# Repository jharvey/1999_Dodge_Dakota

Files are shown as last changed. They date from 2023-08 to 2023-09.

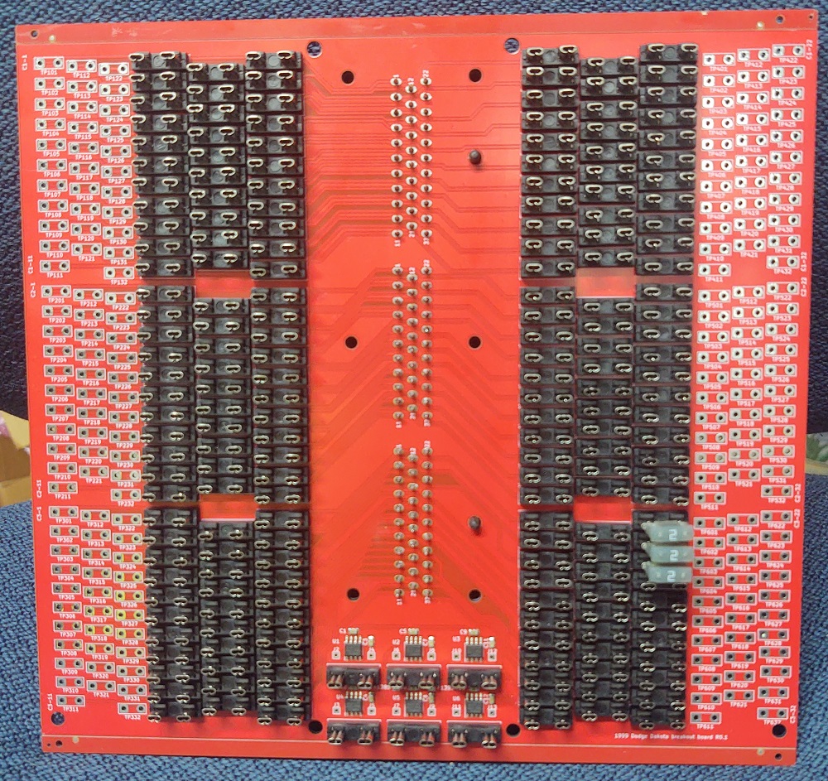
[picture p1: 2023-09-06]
export/Breakout/V0.1/Pictures/Fuse_Side_1000wide.jpg

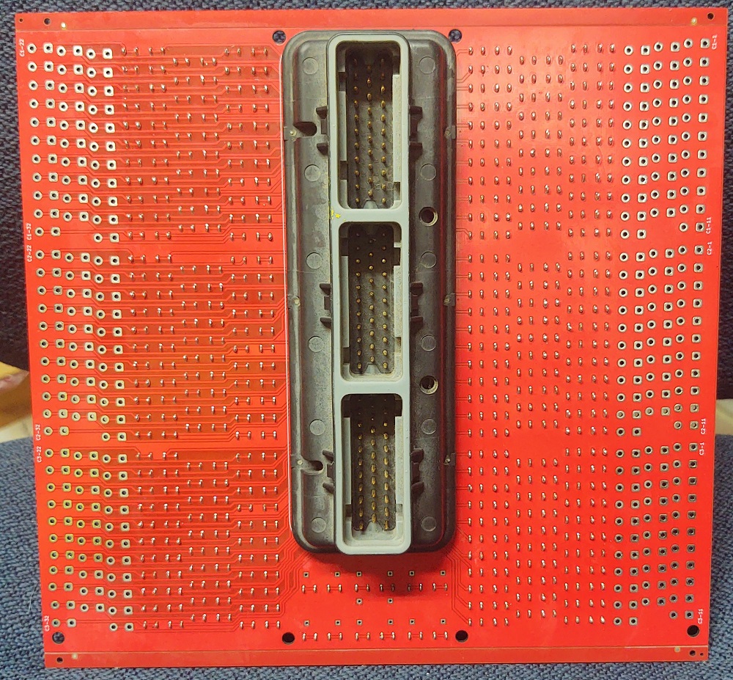
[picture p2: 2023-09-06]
export/Breakout/V0.1/Pictures/Connector_Side_1000wide.jpg

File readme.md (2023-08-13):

#  1999 Dodge Dakota, based on rusEFI PROTEUS

A high-featured board compatible with [rusEFI](https://github.com/rusefi/rusefi) firmware.

# Goals 

- Run my 1999 Dodge Dakota with factory harness and equipment
- Run a sequential ignition, quad-VVT v12 engine (eight injectors, eight ignition, five hall sensors, four VVT actuators, single throttles)
- Easily manufactured sealed enclosure (all connectors mount in-plane)
- Extensible for knock sensing

# Hardware Features

## Microcontroller

- STM32F429ZG
    - 180 MHz ARM Cortex-M7
    - 1MB flash
    - 256 KB SRAM
    - LQFP144 package

- Also fully compatible with several STM32F7 parts, including the STM32F767ZI, used on v0.1 and v0.2, as well as STM32F429ZIT6.

## Connectors
Factory connector for most wiring with TE Connectivity AMPSEAL connector(s) for upgrades:

- 2x 35 pin connectors
    - Board: TE 776231-1 (black, right) and 776231-2 (white, left)
    - Plug: TE 776164-1 (black, right) and 776164-2 (white, left)
- 1x 23 pin connector
    - Board: TE 776228-1
    - Plug: TE 770680-1
- 770854-1 terminals    

## Connectivity

- 1 mbit/s CAN bus
- USB 2.0 full speed (12 mbit/s), on-board or wired to connector for sealed applications
- [10-pin, 1.27mm Cortex debug header](http://infocenter.arm.com/help/topic/com.arm.doc.faqs/attached/13634/cortex_debug_connectors.pdf)

## Outputs
TBD
- 16x 4A low-side drivers
- 12x 5v ignition (or general purpose) outputs
- Dual H-bridges for electronic throttle (also supports stepper idle valve!)
- 4x 12v 3A high-side outputs

## Inputs
TBD
- 11x Analog voltage inputs
- 4x Analog temperature (5v pullup) inputs
- 2x VR crank/cam/vehicle speed inputs
- 6x hall cam/crank or digital input

## Power Supply

- Full operation from 6-24v supply
- Limited operation from 4-6v
- Dual 5v sensor supplies, 150mA each, fully protected
- Dual protected 12v external sensor supply

## Extensibility

- 10-pin internal header for knock expansion board.  We aren't confident in any one knock sensing design yet, so it's most useful to be able to swap it out without replacing the whole ECU.

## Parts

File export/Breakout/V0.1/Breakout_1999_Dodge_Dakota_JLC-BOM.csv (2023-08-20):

Comment | Designator | Footprint | LCSC
100nf | C1,C2,C5,C6,C9,C10 | Capacitor_SMD:C_0805_2012Metric | C49678
1nf | C3,C4,C7,C8,C11,C12 | Capacitor_SMD:C_0805_2012Metric | C46653
Fuse | F1001,F1002,F1003,F1004,F1005,F1006,F1007,F1008,F1009,F1010,F1011,F1012,F1013,F1014,F1015,F1016,F1017,F1018,F1019,F1020,F1021,F1022,F1023,F1024,F1025,F1026,F1027,F1028,F1029,F1030,F1031,F1032,F1033,F1034,F1035,F1036,F1037,F1038,F1039,F1040,F1041,F1042,F1043,F1044,F1045,F1046,F1047,F1048,F1049,F1050,F1051,F1052,F1053,F1054,F1055,F1056,F1057,F1058,F1059,F1060,F1061,F1062,F1063,F1064,F1065,F1066,F1067,F1068,F1069,F1070,F1071,F1072,F1073,F1074,F1075,F1076,F1077,F1078,F1079,F1080,F1081,F1082,F1083,F1084,F1085,F1086,F1087,F1088,F1089,F1090,F1091,F1092,F1093,F1094,F1095,F1096,F1097,F1098,F1099,F1100,F1101,F1102,F1103,F1104,F1105,F1106,F1107,F1108,F1109,F1110,F1111,F1112,F1113,F1114,F1115,F1116,F1117,F1118,F1119,F1120,F1121,F1122,F1123,F1124,F1125,F1126,F1127,F1128,F1129,F1130,F1131,F1132,F1133,F1134,F1135,F1136,F1137,F1138,F1139,F1140,F1141,F1142,F1143,F1144,F1145,F1146,F1147,F1148,F1149,F1150,F1151,F1152,F1153,F1154,F1155,F1156,F1157,F1158,F1159,F1160,F1161,F1162,F1163,F1164,F1165,F1166,F1167,F1168,F1169,F1170,F1171,F1172,F1173,F1174,F1175,F1176,F1177,F1178,F1179,F1180,F1181,F1182,F1183,F1184,F1185,F1186,F1187,F1188,F1189,F1190,F1191,F1192 |  | C151093
Fuse_Holder | F101,F102,F103,F104,F105,F106,F107,F108,F109,F110,F111,F112,F113,F114,F115,F116,F117,F118,F119,F120,F121,F122,F123,F124,F125,F126,F127,F128,F129,F130,F131,F132,F201,F202,F203,F204,F205,F206,F207,F208,F209,F210,F211,F212,F213,F214,F215,F216,F217,F218,F219,F220,F221,F222,F223,F224,F225,F226,F227,F228,F229,F230,F231,F232,F301,F302,F303,F304,F305,F306,F307,F308,F309,F310,F311,F312,F313,F314,F315,F316,F317,F318,F319,F320,F321,F322,F323,F324,F325,F326,F327,F328,F329,F330,F331,F332,F401,F402,F403,F404,F405,F406,F407,F408,F409,F410,F411,F412,F413,F414,F415,F416,F417,F418,F419,F420,F421,F422,F423,F424,F425,F426,F427,F428,F429,F430,F431,F432,F501,F502,F503,F504,F505,F506,F507,F508,F509,F510,F511,F512,F513,F514,F515,F516,F517,F518,F519,F520,F521,F522,F523,F524,F525,F526,F527,F528,F529,F530,F531,F532,F601,F602,F603,F604,F605,F606,F607,F608,F609,F610,F611,F612,F613,F614,F615,F616,F617,F618,F619,F620,F621,F622,F623,F624,F625,F626,F627,F628,F629,F630,F631,F632,F1193,F1194,F1195,F1196,F1197,F1198 | LCSC_parts:LCSC_C2935870_Fuse_holder | C2935870
Pig_Con | J2,J3,J4,J5,J6,J7,J8,J9,J10,J11,J12,J13,F1385,F1393 | TestPoint:TestPoint_THTPad_1.5x1.5mm_Drill0.7mm | NA
Dodge_Con | J1 | Dodge_Cons:1999_Dodge_Connector_32x3cons | NA
TestPoint_2Pole | TP101,TP102,TP103,TP104,TP105,TP106,TP107,TP108,TP109,TP110,TP111,TP112,TP113,TP114,TP115,TP116,TP117,TP118,TP119,TP120,TP121,TP122,TP123,TP124,TP125,TP126,TP127,TP128,TP129,TP130,TP131,TP132,TP201,TP202,TP203,TP204,TP205,TP206,TP207,TP208,TP209,TP210,TP211,TP212,TP213,TP214,TP215,TP216,TP217,TP218,TP219,TP220,TP221,TP222,TP223,TP224,TP225,TP226,TP227,TP228,TP229,TP230,TP231,TP232,TP301,TP302,TP303,TP304,TP305,TP306,TP307,TP308,TP309,TP310,TP311,TP312,TP313,TP314,TP315,TP316,TP317,TP318,TP319,TP320,TP321,TP322,TP323,TP324,TP325,TP326,TP327,TP328,TP329,TP330,TP331,TP332,TP401,TP402,TP403,TP404,TP405,TP406,TP407,TP408,TP409,TP410,TP411,TP412,TP413,TP414,TP415,TP416,TP417,TP418,TP419,TP420,TP421,TP422,TP423,TP424,TP425,TP426,TP427,TP428,TP429,TP430,TP431,TP432,TP501,TP502,TP503,TP504,TP505,TP506,TP507,TP508,TP509,TP510,TP511,TP512,TP513,TP514,TP515,TP516,TP517,TP518,TP519,TP520,TP521,TP522,TP523,TP524,TP525,TP526,TP527,TP528,TP529,TP530,TP531,TP532,TP601,TP602,TP603,TP604,TP605,TP606,TP607,TP608,TP609,TP610,TP611,TP612,TP613,TP614,TP615,TP616,TP617,TP618,TP619,TP620,TP621,TP622,TP623,TP624,TP625,TP626,TP627,TP628,TP629,TP630,TP631,TP632 | TestPoint:TestPoint_2Pads_Pitch5.08mm_Drill1.3mm | NA
ACS712xLCTR-20A | U1,U2,U3,U4,U5,U6 | Package_SO:SOIC-8_3.9x4.9mm_P1.27mm | C10681

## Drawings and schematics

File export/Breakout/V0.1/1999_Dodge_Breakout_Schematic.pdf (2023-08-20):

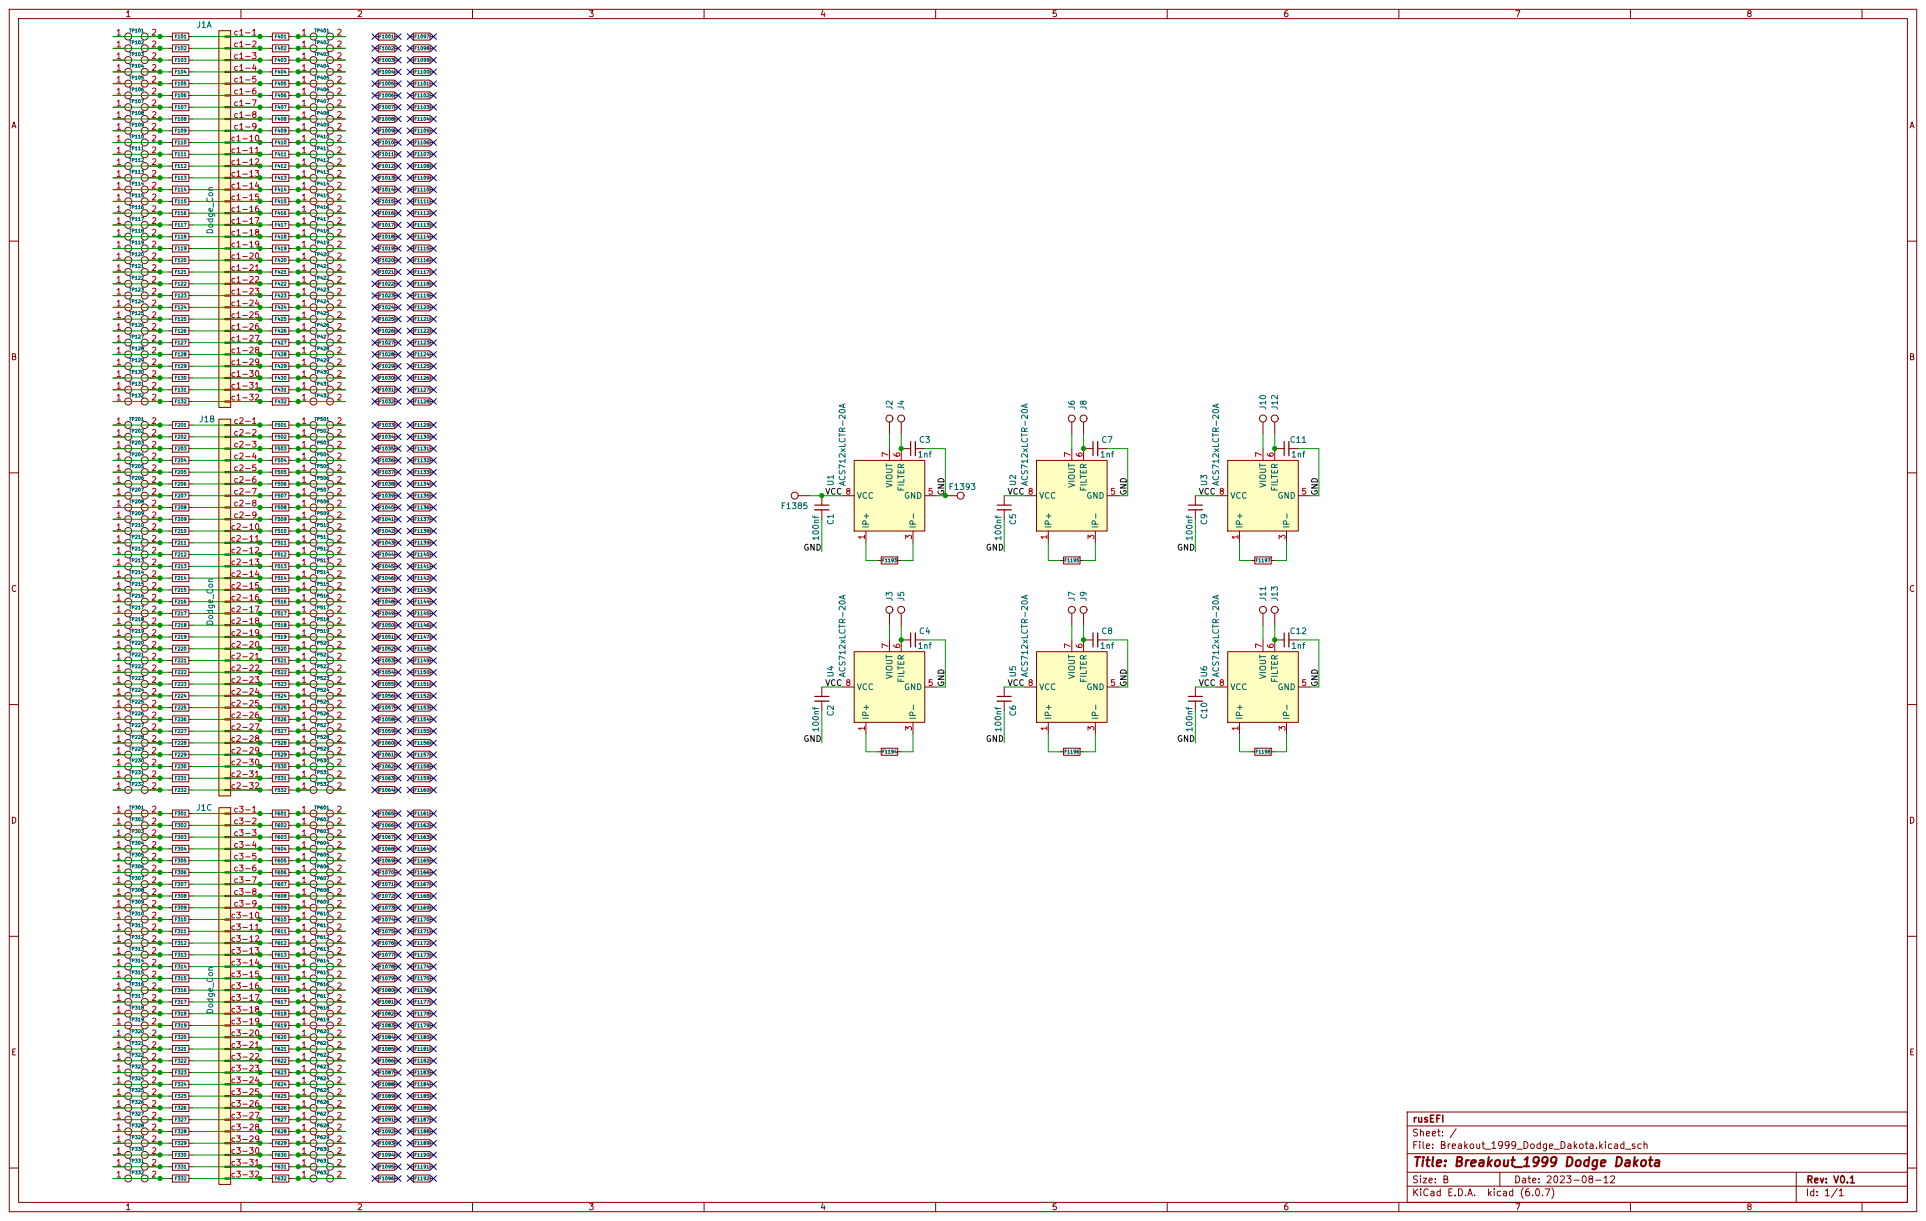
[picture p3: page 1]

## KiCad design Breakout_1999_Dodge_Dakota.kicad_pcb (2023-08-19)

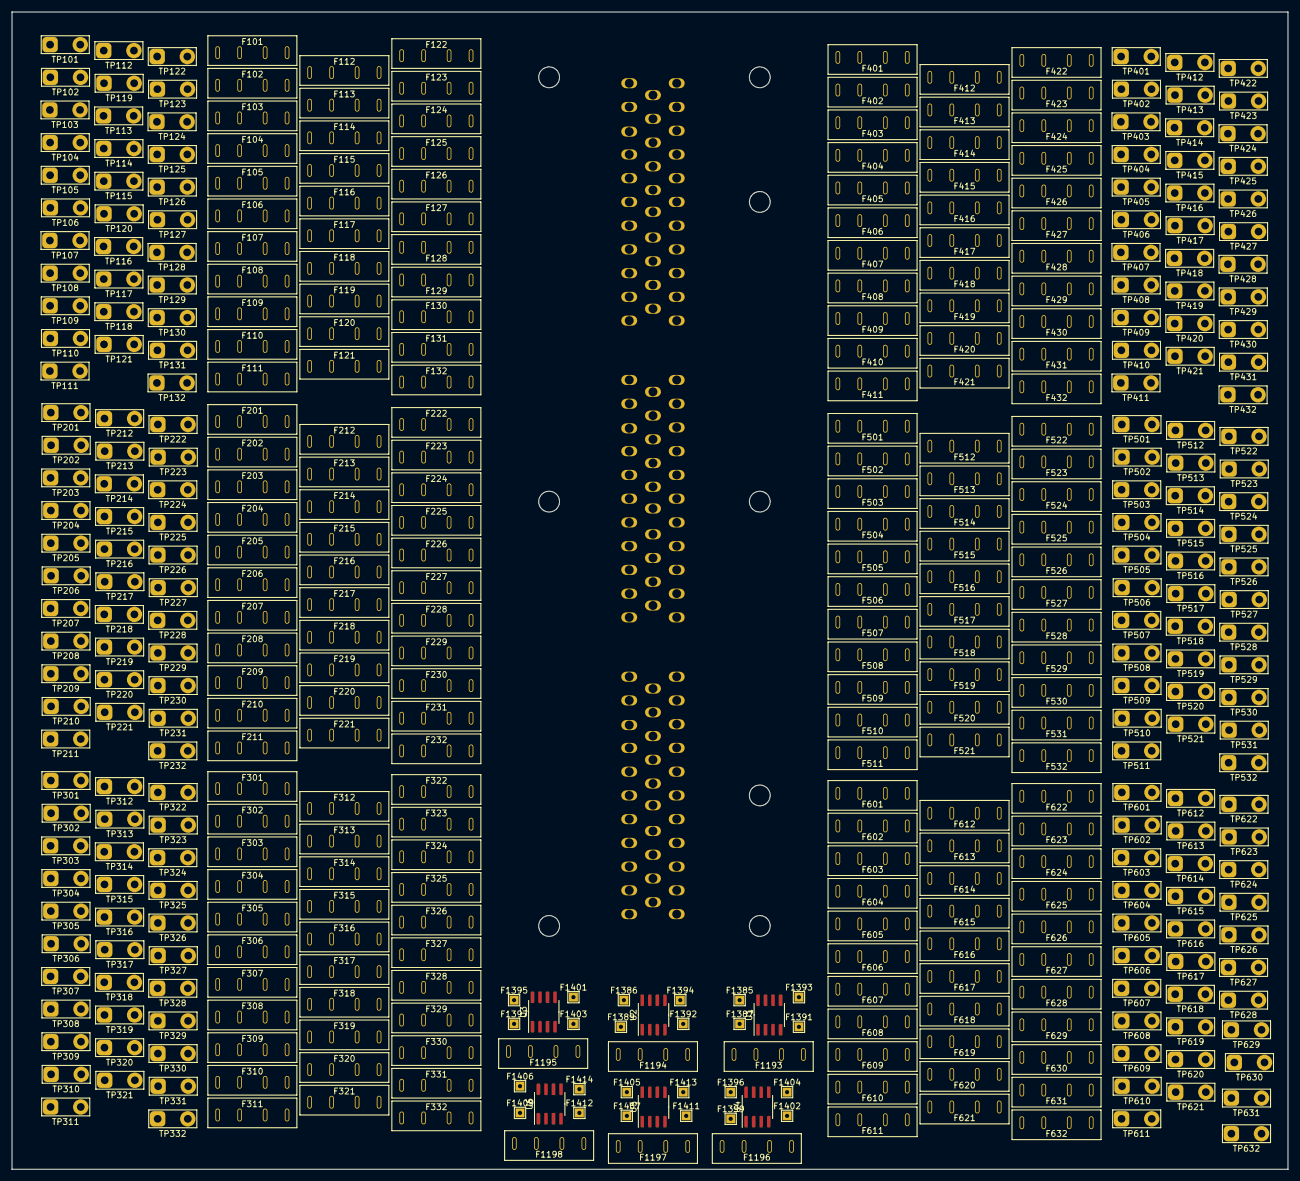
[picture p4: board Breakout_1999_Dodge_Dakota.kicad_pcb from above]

Board: 4 copper layers, 215.0 x 195.0 mm, 421 parts (1 on the bottom side), 324 nets, no tracks yet.

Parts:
F101, F102, F103, F104, F105, F106, F107, F108, F109, F110, F111, F112, F113, F114, F115, F116, F117, F118, F119, F120, F121, F122, F123, F124, F125, F126, F127, F128, F129, F130, F131, F132, F201, F202, F203, F204, F205, F206, F207, F208, F209, F210, F211, F212, F213, F214, F215, F216, F217, F218, F219, F220, F221, F222, F223, F224, F225, F226, F227, F228, F229, F230, F231, F232, F301, F302, F303, F304, F305, F306, F307, F308, F309, F310, F311, F312, F313, F314, F315, F316, F317, F318, F319, F320, F321, F322, F323, F324, F325, F326, F327, F328, F329, F330, F331, F332, F401, F402, F403, F404, F405, F406, F407, F408, F409, F410, F411, F412, F413, F414, F415, F416, F417, F418, F419, F420, F421, F422, F423, F424, F425, F426, F427, F428, F429, F430, F431, F432, F501, F502, F503, F504, F505, F506, F507, F508, F509, F510, F511, F512, F513, F514, F515, F516, F517, F518, F519, F520, F521, F522, F523, F524, F525, F526, F527, F528, F529, F530, F531, F532, F601, F602, F603, F604, F605, F606, F607, F608, F609, F610, F611, F612, F613, F614, F615, F616, F617, F618, F619, F620, F621, F622, F623, F624, F625, F626, F627, F628, F629, F630, F631, F632, F1193, F1194, F1195, F1196, F1197, F1198: Fuse_Holder; LCSC_C2935870_Fuse_holder
F1385, F1386, F1387, F1389, F1391, F1392, F1393, F1394, F1395, F1396, F1397, F1399, F1401, F1402, F1403, F1404, F1405, F1406, F1407, F1409, F1411, F1412, F1413, F1414: Pig_Con; TestPoint_THTPad_1.5x1.5mm_Drill0.7mm
J1: Dodge_Con; 1999_Dodge_Connector_32x3cons
TP101, TP102, TP103, TP104, TP105, TP106, TP107, TP108, TP109, TP110, TP111, TP112, TP113, TP114, TP115, TP116, TP117, TP118, TP119, TP120, TP121, TP122, TP123, TP124, TP125, TP126, TP127, TP128, TP129, TP130, TP131, TP132, TP201, TP202, TP203, TP204, TP205, TP206, TP207, TP208, TP209, TP210, TP211, TP212, TP213, TP214, TP215, TP216, TP217, TP218, TP219, TP220, TP221, TP222, TP223, TP224, TP225, TP226, TP227, TP228, TP229, TP230, TP231, TP232, TP301, TP302, TP303, TP304, TP305, TP306, TP307, TP308, TP309, TP310, TP311, TP312, TP313, TP314, TP315, TP316, TP317, TP318, TP319, TP320, TP321, TP322, TP323, TP324, TP325, TP326, TP327, TP328, TP329, TP330, TP331, TP332, TP401, TP402, TP403, TP404, TP405, TP406, TP407, TP408, TP409, TP410, TP411, TP412, TP413, TP414, TP415, TP416, TP417, TP418, TP419, TP420, TP421, TP422, TP423, TP424, TP425, TP426, TP427, TP428, TP429, TP430, TP431, TP432, TP501, TP502, TP503, TP504, TP505, TP506, TP507, TP508, TP509, TP510, TP511, TP512, TP513, TP514, TP515, TP516, TP517, TP518, TP519, TP520, TP521, TP522, TP523, TP524, TP525, TP526, TP527, TP528, TP529, TP530, TP531, TP532, TP601, TP602, TP603, TP604, TP605, TP606, TP607, TP608, TP609, TP610, TP611, TP612, TP613, TP614, TP615, TP616, TP617, TP618, TP619, TP620, TP621, TP622, TP623, TP624, TP625, TP626, TP627, TP628, TP629, TP630, TP631, TP632: TestPoint_2Pole; TestPoint_2Pads_Pitch5.08mm_Drill1.3mm
U1, U2, U3, U4, U5, U6: ACS712xLCTR-20A; SOIC-8_3.9x4.9mm_P1.27mm

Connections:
unnamed: F101.1, TP101.1, TP101.2
unnamed: F101.2, F401.1, J1.c1-1 (Pin_1)
unnamed: F102.1, TP102.1, TP102.2
unnamed: F102.2, F402.1, J1.c1-2 (Pin_2)
unnamed: F103.1, TP103.1, TP103.2
unnamed: F103.2, F403.1, J1.c1-3 (Pin_3)
unnamed: F104.1, TP104.1, TP104.2
unnamed: F104.2, F404.1, J1.c1-4 (Pin_4)
unnamed: F105.1, TP105.1, TP105.2
unnamed: F105.2, F405.1, J1.c1-5 (Pin_5)
unnamed: F106.1, TP106.1, TP106.2
unnamed: F106.2, F406.1, J1.c1-6 (Pin_6)
unnamed: F107.1, TP107.1, TP107.2
unnamed: F107.2, F407.1, J1.c1-7 (Pin_7)
unnamed: F108.1, TP108.1, TP108.2
unnamed: F108.2, F408.1, J1.c1-8 (Pin_8)
unnamed: F109.1, TP109.1, TP109.2
unnamed: F109.2, F409.1, J1.c1-9 (Pin_9)
unnamed: F110.1, TP110.1, TP110.2
unnamed: F110.2, F410.1, J1.c1-10 (Pin_10)
unnamed: F111.1, TP111.1, TP111.2
unnamed: F111.2, F411.1, J1.c1-11 (Pin_11)
unnamed: F112.1, TP112.1, TP112.2
unnamed: F112.2, F412.1, J1.c1-12 (Pin_12)
unnamed: F113.1, TP113.1, TP113.2
unnamed: F113.2, F413.1, J1.c1-13 (Pin_13)
unnamed: F114.1, TP114.1, TP114.2
unnamed: F114.2, F414.1, J1.c1-14 (Pin_14)
unnamed: F115.1, TP115.1, TP115.2
unnamed: F115.2, F415.1, J1.c1-15 (Pin_15)
unnamed: F116.1, TP116.1, TP116.2
unnamed: F116.2, F416.1, J1.c1-16 (Pin_16)
unnamed: F117.1, TP117.1, TP117.2
unnamed: F117.2, F417.1, J1.c1-17 (Pin_17)
unnamed: F118.1, TP118.1, TP118.2
unnamed: F118.2, F418.1, J1.c1-18 (Pin_18)
unnamed: F119.1, TP119.1, TP119.2
unnamed: F119.2, F419.1, J1.c1-19 (Pin_19)
unnamed: F120.1, TP120.1, TP120.2
unnamed: F120.2, F420.1, J1.c1-20 (Pin_20)
unnamed: F121.1, TP121.1, TP121.2
unnamed: F121.2, F421.1, J1.c1-21 (Pin_21)
unnamed: F122.1, TP122.1, TP122.2
unnamed: F122.2, F422.1, J1.c1-22 (Pin_22)
unnamed: F123.1, TP123.1, TP123.2
unnamed: F123.2, F423.1, J1.c1-23 (Pin_23)
unnamed: F124.1, TP124.1, TP124.2
unnamed: F124.2, F424.1, J1.c1-24 (Pin_24)
unnamed: F125.1, TP125.1, TP125.2
unnamed: F125.2, F425.1, J1.c1-25 (Pin_25)
unnamed: F126.1, TP126.1, TP126.2
unnamed: F126.2, F426.1, J1.c1-26 (Pin_26)
unnamed: F127.1, TP127.1, TP127.2
unnamed: F127.2, F427.1, J1.c1-27 (Pin_27)
unnamed: F128.1, TP128.1, TP128.2
unnamed: F128.2, F428.1, J1.c1-28 (Pin_28)
unnamed: F129.1, TP129.1, TP129.2
unnamed: F129.2, F429.1, J1.c1-29 (Pin_29)
unnamed: F130.1, TP130.1, TP130.2
unnamed: F130.2, F430.1, J1.c1-30 (Pin_30)
unnamed: F131.1, TP131.1, TP131.2
unnamed: F131.2, F431.1, J1.c1-31 (Pin_31)
unnamed: F132.1, TP132.1, TP132.2
unnamed: F132.2, F432.1, J1.c1-32 (Pin_32)
unnamed: F201.1, TP201.1, TP201.2
unnamed: F201.2, F501.1, J1.c2-1 (Pin_1)
unnamed: F202.1, TP202.1, TP202.2
unnamed: F202.2, F502.1, J1.c2-2 (Pin_2)
unnamed: F203.1, TP203.1, TP203.2
unnamed: F203.2, F503.1, J1.c2-3 (Pin_3)
unnamed: F204.1, TP204.1, TP204.2
unnamed: F204.2, F504.1, J1.c2-4 (Pin_4)
unnamed: F205.1, TP205.1, TP205.2
unnamed: F205.2, F505.1, J1.c2-5 (Pin_5)
unnamed: F206.1, TP206.1, TP206.2
unnamed: F206.2, F506.1, J1.c2-6 (Pin_6)
unnamed: F207.1, TP207.1, TP207.2
unnamed: F207.2, F507.1, J1.c2-7 (Pin_7)
unnamed: F208.1, TP208.1, TP208.2
unnamed: F208.2, F508.1, J1.c2-8 (Pin_8)
unnamed: F209.1, TP209.1, TP209.2
unnamed: F209.2, F509.1, J1.c2-9 (Pin_9)
unnamed: F210.1, TP210.1, TP210.2
unnamed: F210.2, F510.1, J1.c2-10 (Pin_10)
unnamed: F211.1, TP211.1, TP211.2
unnamed: F211.2, F511.1, J1.c2-11 (Pin_11)
unnamed: F212.1, TP212.1, TP212.2
unnamed: F212.2, F512.1, J1.c2-12 (Pin_12)
unnamed: F213.1, TP213.1, TP213.2
unnamed: F213.2, F513.1, J1.c2-13 (Pin_13)
unnamed: F214.1, TP214.1, TP214.2
unnamed: F214.2, F514.1, J1.c2-14 (Pin_14)
unnamed: F215.1, TP215.1, TP215.2
unnamed: F215.2, F515.1, J1.c2-15 (Pin_15)
unnamed: F216.1, TP216.1, TP216.2
unnamed: F216.2, F516.1, J1.c2-16 (Pin_16)
unnamed: F217.1, TP217.1, TP217.2
unnamed: F217.2, F517.1, J1.c2-17 (Pin_17)
unnamed: F218.1, TP218.1, TP218.2
unnamed: F218.2, F518.1, J1.c2-18 (Pin_18)
unnamed: F219.1, TP219.1, TP219.2
unnamed: F219.2, F519.1, J1.c2-19 (Pin_19)
unnamed: F220.1, TP220.1, TP220.2
unnamed: F220.2, F520.1, J1.c2-20 (Pin_20)
unnamed: F221.1, TP221.1, TP221.2
unnamed: F221.2, F521.1, J1.c2-21 (Pin_21)
unnamed: F222.1, TP222.1, TP222.2
unnamed: F222.2, F522.1, J1.c2-22 (Pin_22)
unnamed: F223.1, TP223.1, TP223.2
unnamed: F223.2, F523.1, J1.c2-23 (Pin_23)
unnamed: F224.1, TP224.1, TP224.2
unnamed: F224.2, F524.1, J1.c2-24 (Pin_24)
unnamed: F225.1, TP225.1, TP225.2
unnamed: F225.2, F525.1, J1.c2-25 (Pin_25)
unnamed: F226.1, TP226.1, TP226.2
unnamed: F226.2, F526.1, J1.c2-26 (Pin_26)
unnamed: F227.1, TP227.1, TP227.2
unnamed: F227.2, F527.1, J1.c2-27 (Pin_27)
unnamed: F228.1, TP228.1, TP228.2
unnamed: F228.2, F528.1, J1.c2-28 (Pin_28)
unnamed: F229.1, TP229.1, TP229.2
unnamed: F229.2, F529.1, J1.c2-29 (Pin_29)
unnamed: F230.1, TP230.1, TP230.2
unnamed: F230.2, F530.1, J1.c2-30 (Pin_30)
unnamed: F231.1, TP231.1, TP231.2
unnamed: F231.2, F531.1, J1.c2-31 (Pin_31)
unnamed: F232.1, TP232.1, TP232.2
unnamed: F232.2, F532.1, J1.c2-32 (Pin_32)
unnamed: F301.1, TP301.1, TP301.2
unnamed: F301.2, F601.1, J1.c3-1 (Pin_1)
unnamed: F302.1, TP302.1, TP302.2
unnamed: F302.2, F602.1, J1.c3-2 (Pin_2)
unnamed: F303.1, TP303.1, TP303.2
unnamed: F303.2, F603.1, J1.c3-3 (Pin_3)
unnamed: F304.1, TP304.1, TP304.2
unnamed: F304.2, F604.1, J1.c3-4 (Pin_4)
unnamed: F305.1, TP305.1, TP305.2
unnamed: F305.2, F605.1, J1.c3-5 (Pin_5)
unnamed: F306.1, TP306.1, TP306.2
unnamed: F306.2, F606.1, J1.c3-6 (Pin_6)
unnamed: F307.1, TP307.1, TP307.2
unnamed: F307.2, F607.1, J1.c3-7 (Pin_7)
unnamed: F308.1, TP308.1, TP308.2
unnamed: F308.2, F608.1, J1.c3-8 (Pin_8)
unnamed: F309.1, TP309.1, TP309.2
unnamed: F309.2, F609.1, J1.c3-9 (Pin_9)
unnamed: F310.1, TP310.1, TP310.2
unnamed: F310.2, F610.1, J1.c3-10 (Pin_10)
unnamed: F311.1, TP311.1, TP311.2
unnamed: F311.2, F611.1, J1.c3-11 (Pin_11)
unnamed: F312.1, TP312.1, TP312.2
unnamed: F312.2, F612.1, J1.c3-12 (Pin_12)
unnamed: F313.1, TP313.1, TP313.2
unnamed: F313.2, F613.1, J1.c3-13 (Pin_13)
unnamed: F314.1, TP314.1, TP314.2
unnamed: F314.2, F614.1, J1.c3-14 (Pin_14)
unnamed: F315.1, TP315.1, TP315.2
unnamed: F315.2, F615.1, J1.c3-15 (Pin_15)
unnamed: F316.1, TP316.1, TP316.2
unnamed: F316.2, F616.1, J1.c3-16 (Pin_16)
unnamed: F317.1, TP317.1, TP317.2
unnamed: F317.2, F617.1, J1.c3-17 (Pin_17)
unnamed: F318.1, TP318.1, TP318.2
unnamed: F318.2, F618.1, J1.c3-18 (Pin_18)
unnamed: F319.1, TP319.1, TP319.2
unnamed: F319.2, F619.1, J1.c3-19 (Pin_19)
unnamed: F320.1, TP320.1, TP320.2
unnamed: F320.2, F620.1, J1.c3-20 (Pin_20)
unnamed: F321.1, TP321.1, TP321.2
unnamed: F321.2, F621.1, J1.c3-21 (Pin_21)
unnamed: F322.1, TP322.1, TP322.2
unnamed: F322.2, F622.1, J1.c3-22 (Pin_22)
unnamed: F323.1, TP323.1, TP323.2
unnamed: F323.2, F623.1, J1.c3-23 (Pin_23)
unnamed: F324.1, TP324.1, TP324.2
unnamed: F324.2, F624.1, J1.c3-24 (Pin_24)
unnamed: F325.1, TP325.1, TP325.2
unnamed: F325.2, F625.1, J1.c3-25 (Pin_25)
unnamed: F326.1, TP326.1, TP326.2
unnamed: F326.2, F626.1, J1.c3-26 (Pin_26)
unnamed: F327.1, TP327.1, TP327.2
unnamed: F327.2, F627.1, J1.c3-27 (Pin_27)
unnamed: F328.1, TP328.1, TP328.2
unnamed: F328.2, F628.1, J1.c3-28 (Pin_28)
unnamed: F329.1, TP329.1, TP329.2
unnamed: F329.2, F629.1, J1.c3-29 (Pin_29)
unnamed: F330.1, TP330.1, TP330.2
unnamed: F330.2, F630.1, J1.c3-30 (Pin_30)
unnamed: F331.1, TP331.1, TP331.2
unnamed: F331.2, F631.1, J1.c3-31 (Pin_31)
unnamed: F332.1, TP332.1, TP332.2
unnamed: F332.2, F632.1, J1.c3-32 (Pin_32)
unnamed: F401.2, TP401.1, TP401.2
unnamed: F402.2, TP402.1, TP402.2
unnamed: F403.2, TP403.1, TP403.2
unnamed: F404.2, TP404.1, TP404.2
unnamed: F405.2, TP405.1, TP405.2
unnamed: F406.2, TP406.1, TP406.2
unnamed: F407.2, TP407.1, TP407.2
unnamed: F408.2, TP408.1, TP408.2
unnamed: F409.2, TP409.1, TP409.2
unnamed: F410.2, TP410.1, TP410.2
unnamed: F411.2, TP411.1, TP411.2
unnamed: F412.2, TP412.1, TP412.2
unnamed: F413.2, TP413.1, TP413.2
unnamed: F414.2, TP414.1, TP414.2
unnamed: F415.2, TP415.1, TP415.2
unnamed: F416.2, TP416.1, TP416.2
unnamed: F417.2, TP417.1, TP417.2
unnamed: F418.2, TP418.1, TP418.2
unnamed: F419.2, TP419.1, TP419.2
unnamed: F420.2, TP420.1, TP420.2
unnamed: F421.2, TP421.1, TP421.2
unnamed: F422.2, TP422.1, TP422.2
unnamed: F423.2, TP423.1, TP423.2
unnamed: F424.2, TP424.1, TP424.2
unnamed: F425.2, TP425.1, TP425.2
unnamed: F426.2, TP426.1, TP426.2
unnamed: F427.2, TP427.1, TP427.2
unnamed: F428.2, TP428.1, TP428.2
unnamed: F429.2, TP429.1, TP429.2
unnamed: F430.2, TP430.1, TP430.2
unnamed: F431.2, TP431.1, TP431.2
unnamed: F432.2, TP432.1, TP432.2
unnamed: F501.2, TP501.1, TP501.2
unnamed: F502.2, TP502.1, TP502.2
unnamed: F503.2, TP503.1, TP503.2
unnamed: F504.2, TP504.1, TP504.2
unnamed: F505.2, TP505.1, TP505.2
unnamed: F506.2, TP506.1, TP506.2
unnamed: F507.2, TP507.1, TP507.2
unnamed: F508.2, TP508.1, TP508.2
unnamed: F509.2, TP509.1, TP509.2
unnamed: F510.2, TP510.1, TP510.2
unnamed: F511.2, TP511.1, TP511.2
unnamed: F512.2, TP512.1, TP512.2
unnamed: F513.2, TP513.1, TP513.2
unnamed: F514.2, TP514.1, TP514.2
unnamed: F515.2, TP515.1, TP515.2
unnamed: F516.2, TP516.1, TP516.2
unnamed: F517.2, TP517.1, TP517.2
unnamed: F518.2, TP518.1, TP518.2
unnamed: F519.2, TP519.1, TP519.2
unnamed: F520.2, TP520.1, TP520.2
unnamed: F521.2, TP521.1, TP521.2
unnamed: F522.2, TP522.1, TP522.2
unnamed: F523.2, TP523.1, TP523.2
unnamed: F524.2, TP524.1, TP524.2
unnamed: F525.2, TP525.1, TP525.2
unnamed: F526.2, TP526.1, TP526.2
unnamed: F527.2, TP527.1, TP527.2
unnamed: F528.2, TP528.1, TP528.2
unnamed: F529.2, TP529.1, TP529.2
unnamed: F530.2, TP530.1, TP530.2
unnamed: F531.2, TP531.1, TP531.2
unnamed: F532.2, TP532.1, TP532.2
unnamed: F601.2, TP601.1, TP601.2
unnamed: F602.2, TP602.1, TP602.2
unnamed: F603.2, TP603.1, TP603.2
unnamed: F604.2, TP604.1, TP604.2
unnamed: F605.2, TP605.1, TP605.2
unnamed: F606.2, TP606.1, TP606.2
unnamed: F607.2, TP607.1, TP607.2
unnamed: F608.2, TP608.1, TP608.2
unnamed: F609.2, TP609.1, TP609.2
unnamed: F610.2, TP610.1, TP610.2
unnamed: F611.2, TP611.1, TP611.2
unnamed: F612.2, TP612.1, TP612.2
unnamed: F613.2, TP613.1, TP613.2
unnamed: F614.2, TP614.1, TP614.2
unnamed: F615.2, TP615.1, TP615.2
unnamed: F616.2, TP616.1, TP616.2
unnamed: F617.2, TP617.1, TP617.2
unnamed: F618.2, TP618.1, TP618.2
unnamed: F619.2, TP619.1, TP619.2
unnamed: F620.2, TP620.1, TP620.2
unnamed: F621.2, TP621.1, TP621.2
unnamed: F622.2, TP622.1, TP622.2
unnamed: F623.2, TP623.1, TP623.2
unnamed: F624.2, TP624.1, TP624.2
unnamed: F625.2, TP625.1, TP625.2
unnamed: F626.2, TP626.1, TP626.2
unnamed: F627.2, TP627.1, TP627.2
unnamed: F628.2, TP628.1, TP628.2
unnamed: F629.2, TP629.1, TP629.2
unnamed: F630.2, TP630.1, TP630.2
unnamed: F631.2, TP631.1, TP631.2
unnamed: F632.2, TP632.1, TP632.2
unnamed: F1193.1, U1.3 (IP-), U1.4 (IP-)
unnamed: F1193.2, U1.1 (IP+), U1.2 (IP+)
unnamed: F1194.1, U2.3 (IP-), U2.4 (IP-)
unnamed: F1194.2, U2.1 (IP+), U2.2 (IP+)
unnamed: F1195.1, U3.3 (IP-), U3.4 (IP-)
unnamed: F1195.2, U3.1 (IP+), U3.2 (IP+)
unnamed: F1196.1, U4.3 (IP-), U4.4 (IP-)
unnamed: F1196.2, U4.1 (IP+), U4.2 (IP+)
unnamed: F1197.1, U5.3 (IP-), U5.4 (IP-)
unnamed: F1197.2, U5.1 (IP+), U5.2 (IP+)
unnamed: F1198.1, U6.3 (IP-), U6.4 (IP-)
unnamed: F1198.2, U6.1 (IP+), U6.2 (IP+)
unnamed: F1385.1, U1.8 (VCC)
unnamed: F1386.1, U2.8 (VCC)
unnamed: F1387.1, U1.7 (VIOUT)
unnamed: F1389.1, U2.7 (VIOUT)
unnamed: F1391.1, U1.6 (FILTER)
unnamed: F1392.1, U2.6 (FILTER)
unnamed: F1393.1, U1.5 (GND)
unnamed: F1394.1, U2.5 (GND)
unnamed: F1395.1, U3.8 (VCC)
unnamed: F1396.1, U4.8 (VCC)
unnamed: F1397.1, U3.7 (VIOUT)
unnamed: F1399.1, U4.7 (VIOUT)
unnamed: F1401.1, U3.6 (FILTER)
unnamed: F1402.1, U4.6 (FILTER)
unnamed: F1403.1, U3.5 (GND)
unnamed: F1404.1, U4.5 (GND)
unnamed: F1405.1, U5.8 (VCC)
unnamed: F1406.1, U6.8 (VCC)
unnamed: F1407.1, U5.7 (VIOUT)
unnamed: F1409.1, U6.7 (VIOUT)
unnamed: F1411.1, U5.6 (FILTER)
unnamed: F1412.1, U6.6 (FILTER)
unnamed: F1413.1, U5.5 (GND)
unnamed: F1414.1, U6.5 (GND)

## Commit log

2023-08-13 Updated symbols to KC7 links for C17, C1001, D1, D2, FB1501, JP1201, 3.3V Updated symbols to KC7 links and made minor adjustments to wires for JP1 and JP2 Deleted unused rescue files.
    [etb-9201.kicad_sch, etb-9201.sch, highside_quad.kicad_sch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]
2023-08-13 File names changed / moved to folders. Updated file names to 1999_Dodge_Dakota Moved files footprints and symbols into a folder
    [1999_Dodge_Dakota.kicad_sch, boardout.kicad_pcb, boardout.sch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]
2023-08-19 Draft breakout board check in.
    [1999_Dodge_Dakota.kicad_sch, Breakout_1999_Dodge_Dakota.kicad_pcb, Breakout_1999_Dodge_Dakota.kicad_sch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]
2023-08-19 Another draft check in. Deleted unused "export" files.
    [Breakout_1999_Dodge_Dakota.kicad_pcb, Breakout_1999_Dodge_Dakota.kicad_sch, Proteus_case_lid_DC-45.dwg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]
2023-08-20 Draft commit, mostly routed, silk screen needs work. Passes ERC and DRC
    [Breakout_1999_Dodge_Dakota.kicad_sch]
2023-08-20 Breakout V0.1 Checked in.
    [Breakout_1999_Dodge_Dakota_JLC-BOM.csv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]
2023-09-07 Made slight changes to screw holes and 3D model per first built. Moved holes 0.5mm.
2023-09-08 Added URL to connector 3D model.
